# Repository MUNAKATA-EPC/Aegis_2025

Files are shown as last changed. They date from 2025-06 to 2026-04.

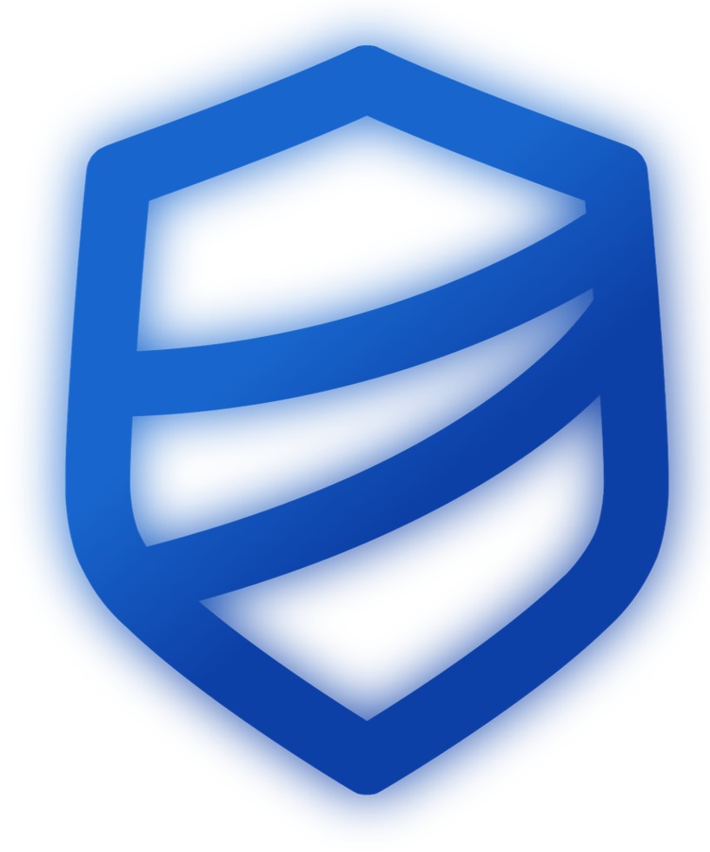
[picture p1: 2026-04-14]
2025/Salvador/presentation sheet material/画像6.jpg

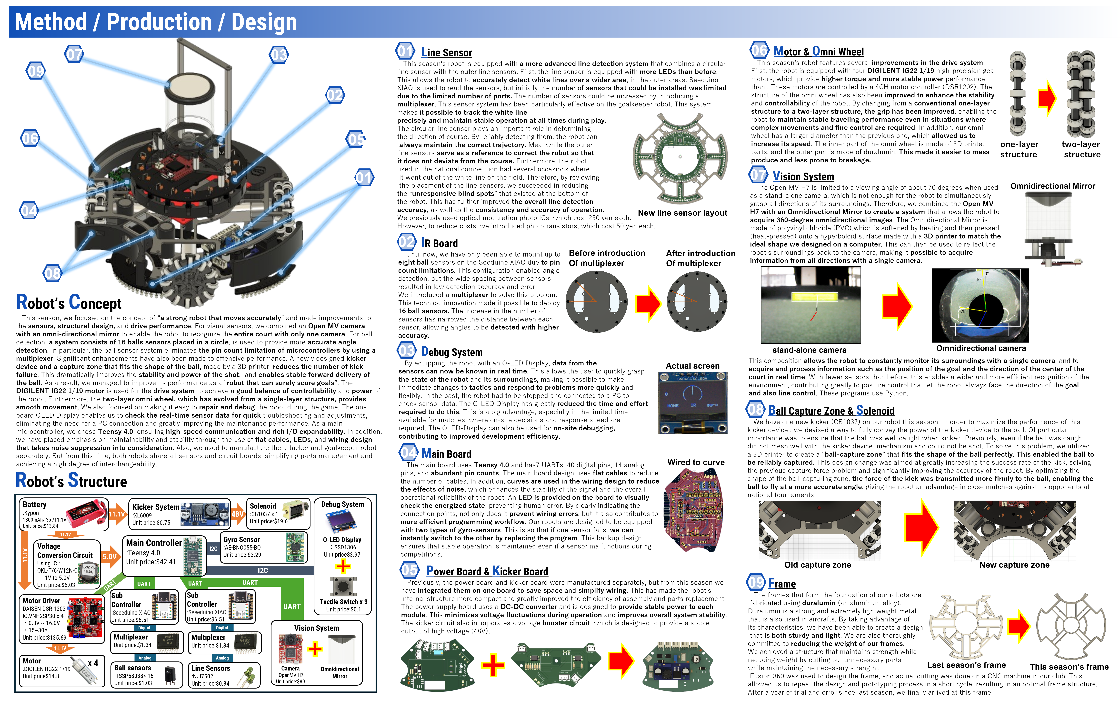
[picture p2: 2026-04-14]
2025/Salvador/presentation sheet material/英語 めっそど.png

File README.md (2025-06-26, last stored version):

🏆 Competition Results

<2024 Season>
Kitakyushu Node Tournament → 🥇 Champion (A Court)

Kyushu Block Tournament → 🥇 Champion, 🏅 Best Presentation Award

Japan Open 2024 Soccer Lightweight League → 31st place

<2025 Season>
Fukuoka Node Tournament → 🥇 Champion

Kyushu Block Tournament → 🥇 Champion

Japan Open 2025 Soccer Lightweight League → 🥇 Champion, 🏅 Best Presentation Award

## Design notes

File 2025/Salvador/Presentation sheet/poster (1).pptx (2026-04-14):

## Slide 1

Munako Artemis
Munakata High School

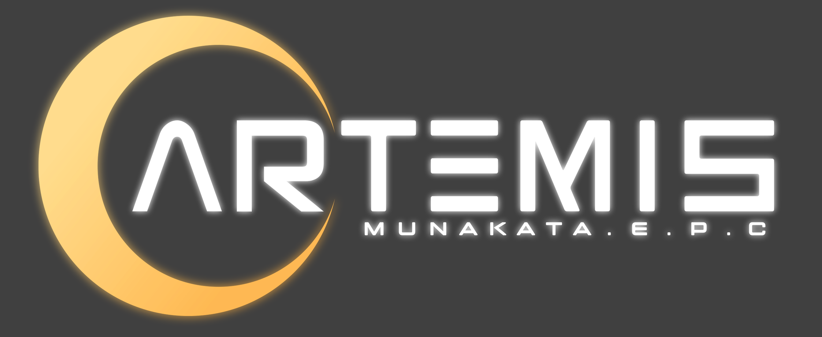
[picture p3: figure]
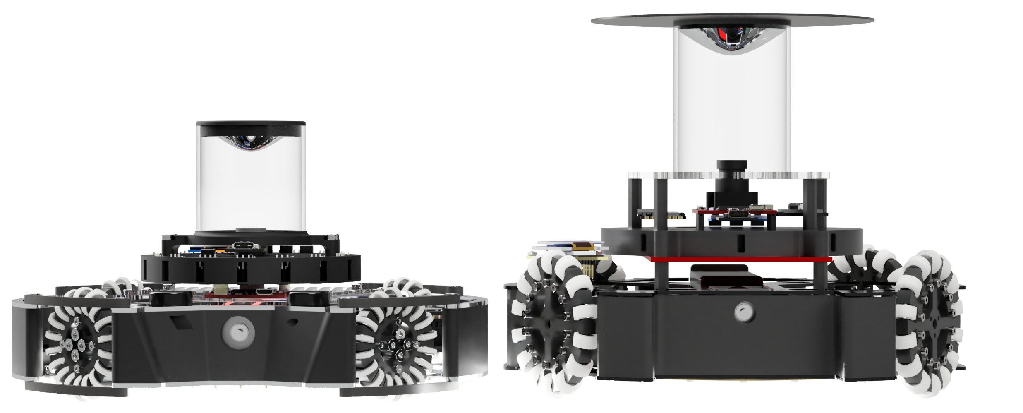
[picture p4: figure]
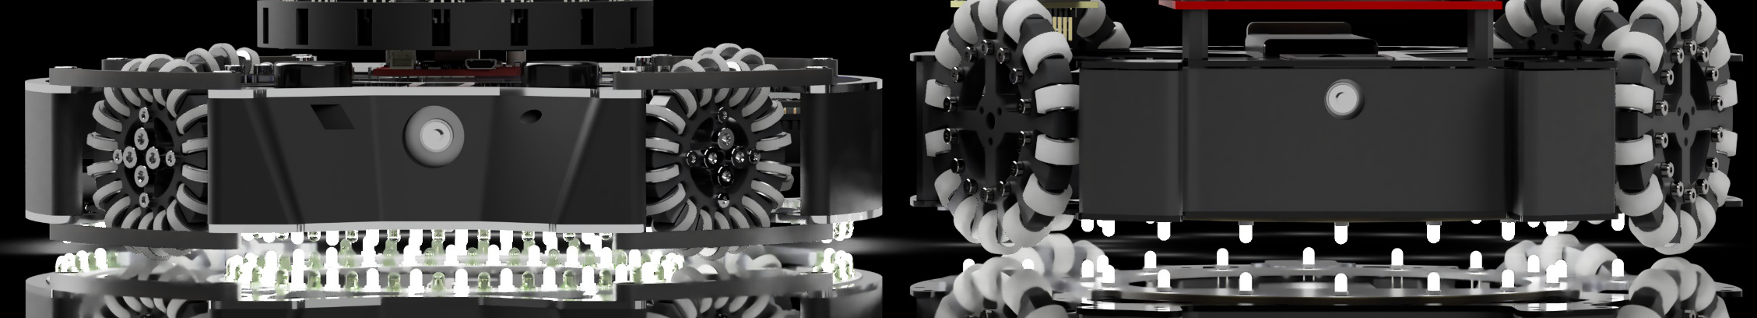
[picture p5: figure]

Abstract

Munako Artemis is a Japanese team participating in Soccer LWL. The team consists of four high school students and has been active since 2021.
For robot design, we mainly use Autodesk Fusion, and for circuit design, we use KiCad. By utilizing 3D printers and CNC milling machines, we efficiently created our robots. Almost all the sensors and microcontrollers are the same among both of our robots, simplifying parts management and increasing compatibility. Additionally, the programming is primarily done in C++ for most microcontrollers and in MicroPython for the camera.
In preparation for the world tournament, we made modifications to our robots to address various issues identified in the Japan Open 2024. One significant problem was the frequent occurrence of out-of-bounds, so we improved the shape of the line sensors from a linear to a circular design and changed the sensor processing algorithm. Additionally, we often had difficulty carrying the ball forward, so we expanded the ball-capturing zone to make it easier to capture the ball and improved the ball-tracking algorithm.
Both of our robots are equipped with a kicker mechanism that uses a solenoid to kick the ball. However, we had no idea which voltage and capacitor capacity would result in the strongest kick. Therefore, we investigated how the kicking power changes with different voltages and capacitor capacities and created graphs to determine the optimal settings for the strongest kick.
Although this is our first time participating in a world tournament, we are strongly motivated by the desire to "interact with various people, acquire diverse knowledge, and gain valuable experiences." To share our knowledge with a wider audience, we have created a website and social media accounts.

REGION

JAPAN

Method / Production / Design

【Robots’ Overview / Descriptions Of The Installed Parts 】

Robot.2's concept is to be a "strong robot with stable operation" for soccer competitions, which is a challenging feat to achieve. However, we have implemented various innovations to achieve this goal.
All components installed in Robot.2 have undergone a year-long development and testing process to ensure stability. Additionally, it is designed to place various additional components for adapting to changes in rules.
By completing the robot production process early and allowing sufficient time for adjustments, we can achieve stable operation and develop a "strong robot".

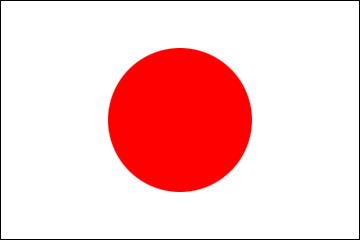
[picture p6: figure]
国旗・国歌」について - 内閣府

LEAGUE

Soccer LWL

Team Member

Kyle Matsuda : Hardware
Yuki Meno : Hardware
Rentaro Ishihara : Software
Ryota Kumadaki : Software

Team Website
https://munako-artemis.github.io/
Team X(Twitter)
https://x.com/munako_artemis
Team GitHub
https://github.com/MUNAKATA-EPC

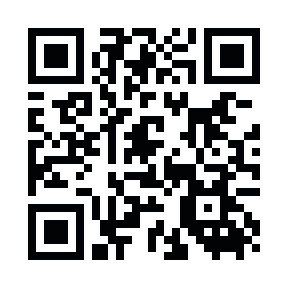
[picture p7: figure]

Website

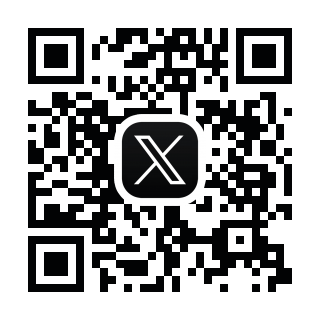
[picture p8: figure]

X(Twitter)

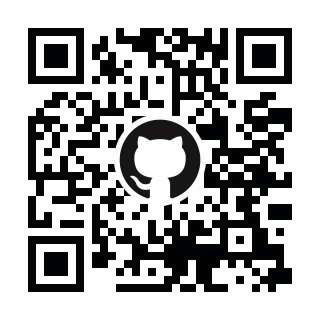
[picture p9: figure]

GitHub

SPONSERS

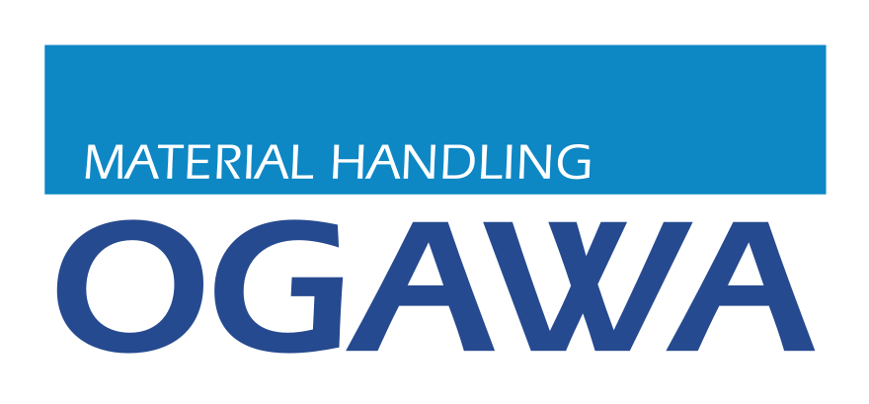
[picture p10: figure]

Robot.1's concept is to be a "robot with a low center of gravity and high maintenance performance". In a robot that moves freely around the court at high speed, having a low center of gravity is crucial. A low center of gravity allows the robot to execute turns and speed changes with minimal force, reducing power consumption and enabling more precise movements.
However, achieving a low center of gravity often means designing the robot to be compact and densely packed with components internally, potentially compromising maintenance accessibility.
To address this challenge, Robot.1 has been designed with a reduced number of components.
Most parts and boards can be quickly removed and replaced, ensuring ease of maintenance despite its low-profile design.

【Robots’ Features】

> Improvement of the shape of the Line Sensor
During the Japan Open 2024, we identified the following issues with our line sensors:
・It was taking too much time for the sensors to detect the white line after the robot has crossed it.
・Poor color compatibility between the sensors and the white line leads to erroneous detections.
To address these issues, we implemented the following improvements.
・Changing the type of the Sensor
As we mentioned earlier, poor color compatibility between the sensors and the white line leaded to erroneous detections, so we have changed the sensor to NJL7502S. By changing the sensor, we can sufficiently detect the difference in response between white and green, enabling us to detect white lines and reduce occurrences of out-of-bounds.
・Changing the shape of the line sensor (Fig.A)
We added new sensors to the left, right, and rear in addition to the central circular line sensor. This allows the robot to immediately detect the white line when it crosses over it.
・Increasing the number of the sensor ports
For the circular line sensor, reading values from each sensor allows us to estimate the current position of the reacting white line.

Fig.A a shape of line sensor
(Robot.1)

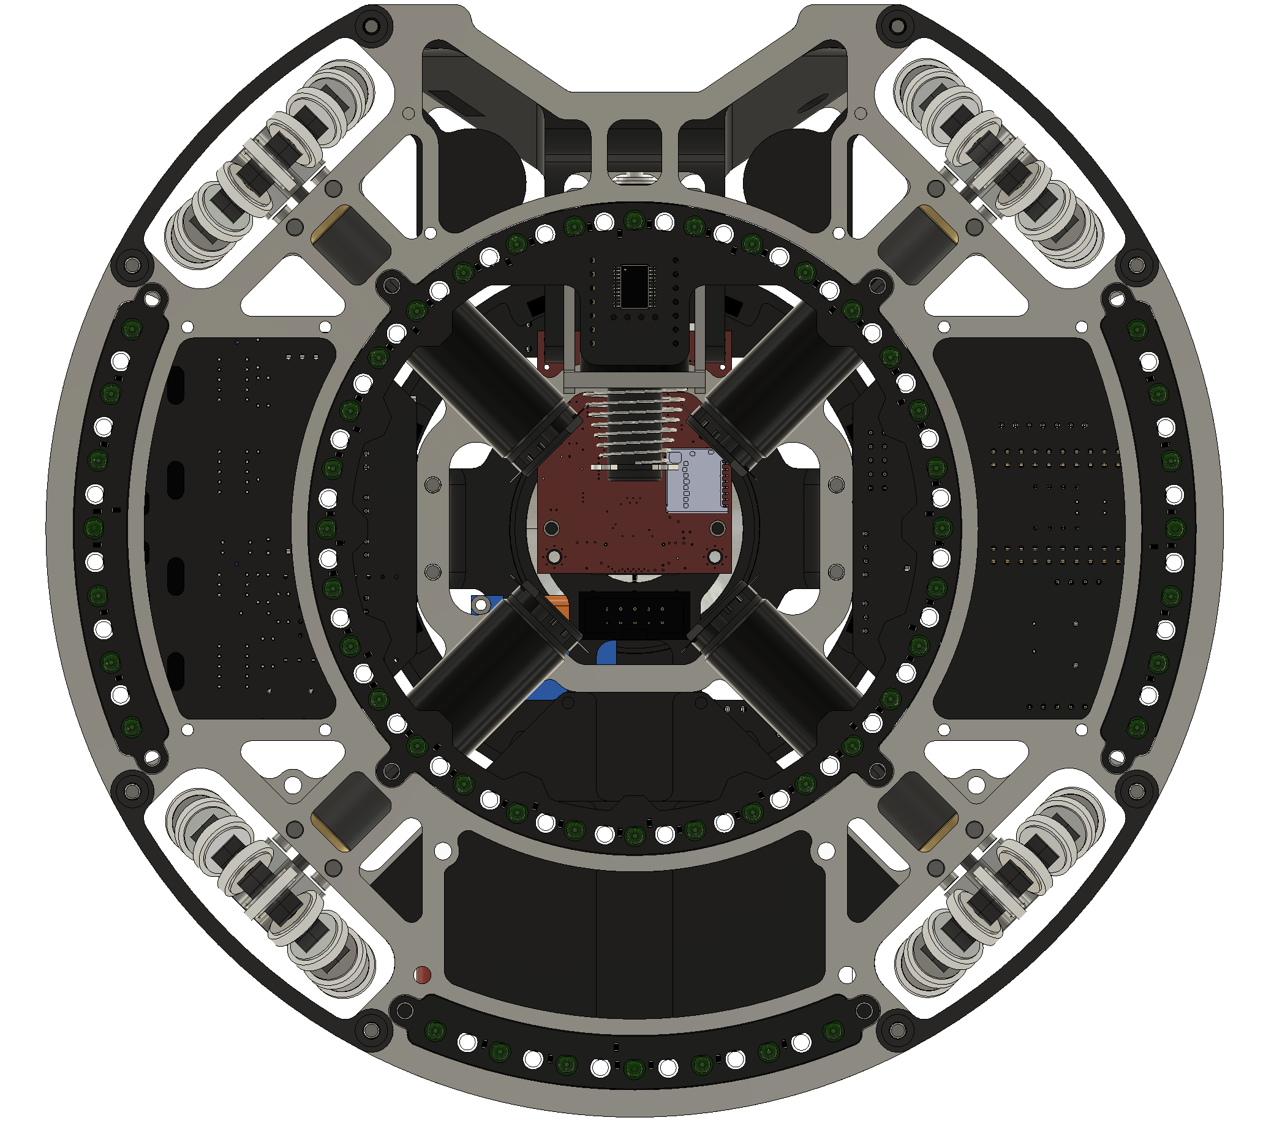
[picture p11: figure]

Ball Angle

Move
Direction

90°

90°

90°

Fig.B-1 ball-tracking system when ball is near

X°

Fig.B-2 ball-tracking system when ball is far

1 Omnidirectional Vision System
We have positioned the camera facing upwards and placed an omnidirectional mirror at the top of an acrylic pipe.
By doing this, we can capture a 360-degree view from the robot without using multiple cameras, significantly simplifying control compared to using multiple cameras.
We are using OpenMV as camera module. It is programmed with MicroPython.

Debugging Components
We have placed menu operation buttons and a small LCD monitor at the rear of the robot.
These are positioned for easy access during a match, allowing us to check sensor values and change the robot’s
Mode without connecting to a computer.

1

Robo.1

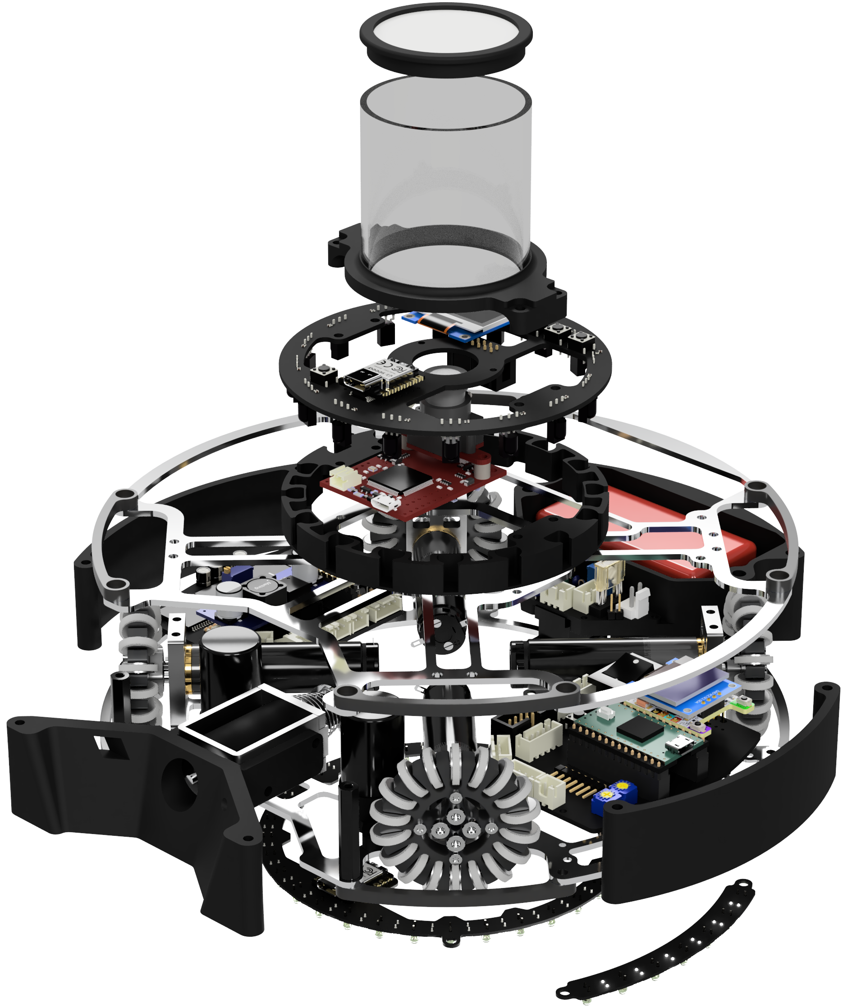
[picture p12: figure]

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
A. Main Board (Robot.1)
This board is equipped with the “Teensy 4.0” main microcontroller, the “BNO055” IMU sensor, the “Twelite UART” communication module for inter-robot communication, the tournament’s official communication module, and various control switches.
All of the data from microcontrollers and sensors on other boards is aggregated here, and this data is used to control the robot.
・Teensy 4.0 : It has many serial ports and very high performance, making it suitable for high-precision control using many sensors and sub-microcontrollers.
・BNO055 : It allows easy control and has less angular drift compared to other IMU sensors.
・Twelite : It enables easy communication by simply connecting it to the microcontroller via UART.

A

3. Ball Capture Detecting Sensor
We have placed an LED on one side of the ball supplement area, and an S4282-51 photodetector IC on the other side, which detects the ball supplement.
This IC responds only to light of a frequency synchronized with the IC itself, allowing it to be used even in daylight or under an indoor lighting without causing false detections, making it ideal for precise control.

4. IR Sensor
We have chosen the TSSP58038 for the ball detection. By placing 16 of them in a circular pattern on the central board, we can calculate the angle of the ball more accurately.

2

3

B. Drive Board (Robot.1)
This board incorporates a motor driver circuit and a kicker drive circuit.
We have chosen VNH5019 for the motor driver IC, and XL6009 for the voltage booster included to de kicker circuit.
The motor driver IC can handle a power supply voltage of up to 41V, which is more than three times the voltage supplied from the battery, and it supports an extremely high current of 30A, ensuring high durability.
The kicker circuit uses two types of MOSFETs, P-channel and N-channel. One is used for controlling the solenoid, and the other is used to disconnect the circuit during the kick motion.
By isolating the kicker circuit from other circuits during kicking, we can physically block the electrical noise caused by the voltage drop during the kicking motion and the back electromotive force generated when the solenoid's shaft returns.
This ensures that no noise affects both the driving power supply and the control power supply.

C. Main Board (Robot.2)
This board is equipped with a Teensy 4.0 as the main microcontroller, an L3GD20H and a BNO055 as IMU sensors, an OpenMV camera, an SSD1306 display, and TSSP58038 sensors for ball detection.
There are eight IR sensors installed to calculate the ball's angle using vector processing.
Two gyro sensors are installed to ensure redundancy in case one fails during the match.
Additionally, the display allows us to check the sensor values and to change the robot's mode without connecting it to a computer, making adjustments to the robot more easily.

B

> Improvement of Ball Access Time
through Ball Tracking Algorithm Enhancement
During the national competition, we identified the following issues with our ball tracking algorithm: Lack of distance-based control between the robot and the ball resulted in excessive rounding, leading to delayed ball access.
To address these issues, we developed the following ball tracking algorithm:
In the diagram on the right, we define Ball Angle as the angle of the ball relative to the robot, and Move Direction as the actual angle of movement of the robot.
A. When the robot is close to the ball (Fig.B-1)
Move in the tangential direction to the ball (= Ball Angle + 90) to approach the ball.
B. When the robot is far from the ball (Fig.B-2)
Add a constant (= Ball Angle + X) to move towards the ball.
By doing these, the robot can approach to it shorter way than before, and colliding with the ball is almost nothing, so own-goal was decreasing.

> Line Tracing Defense Using Circular Line Sensors
Our robot is equipped with circular line sensors, which we utilize for goal defense through line tracing. The defense system is illustrated in Fig.C.
It uses the perpendicular line to the line connecting the two line sensors reacting to the white line as the reference line.
In case ①, when the angle of the ball and the reference line have a small error, the robot stops to block the shot from an oblique direction.
In case ②, when the angle of the ball and the reference line have a large error, the robot moves in the direction of the line sensor detecting the ball, keeping it on the white line while moving towards the ball to block the shot.

By combining these movements in cases ① and ②, the robot can effectively prevent the ball from entering the goal.

Line Sensor
We have positioned a circular board in the center and a board with a circular cut-out shape on the outer edge. The description about the line sensor is summarized in
“Robot’s Feature” section.

6. Power Circuit Board
The power circuit board includes battery protection circuits, and circuits for generating both the drive power supply and control power supply.
The battery protection circuits feature reverse connection protection, overcurrent protection, and over-discharge prevention.
To generate the control power supply, a DC-DC converter is used, which minimizes the electrical noise from the drive power supply, ensuring stable operation of the microcontrollers.

4

5

6

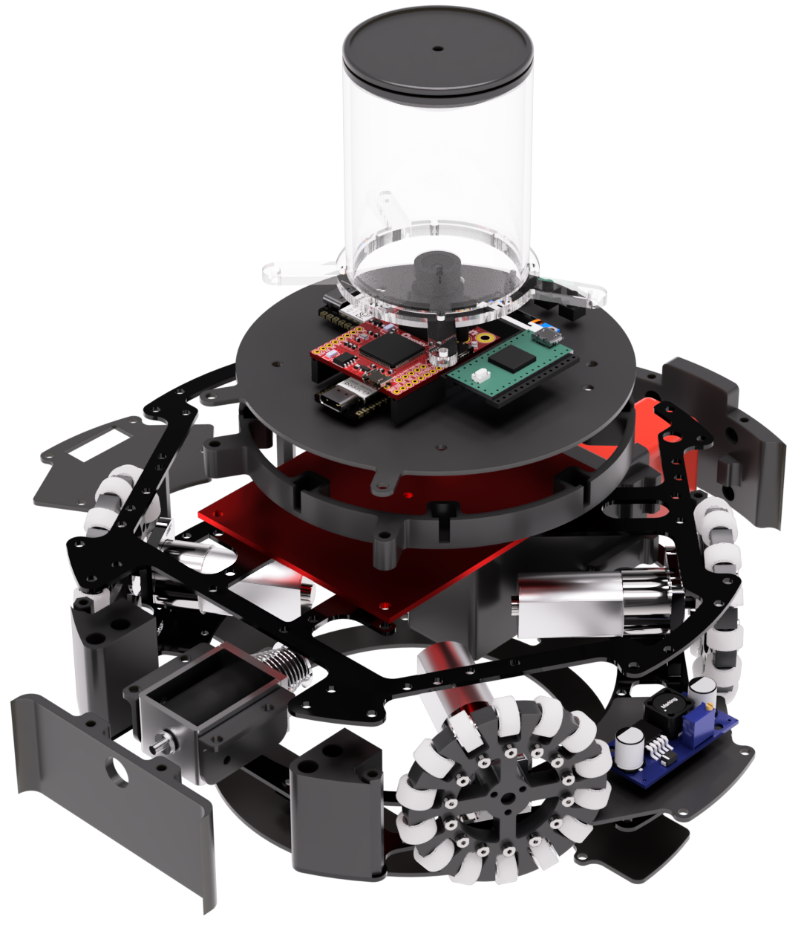
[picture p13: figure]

Robo.2

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
Our Robots’ Structure

Robo.1

Battery
Kypom 3S 11.1V
1300mAh

Gyro Sensor
BNO055

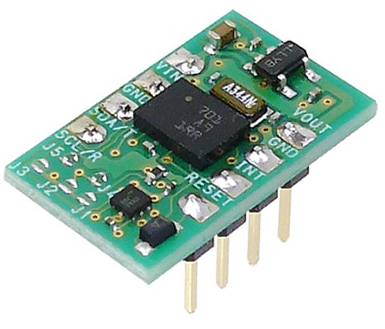
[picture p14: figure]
BNO055使用 9軸センサーフュージョンモジュールキット

11.1V

Voltage Conversion Circuit
Using IC :
OKL-T/6-W12N-C
11.1V to 5.0V

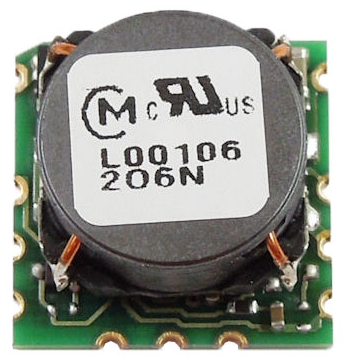
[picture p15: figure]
ムラタ表面実装DC-DCコンバーター OKL-T/6-W12N-C

Drive Circuit Board : Kicker System And Motor Driver

Kicker System
(Please look at
“Kicker System And Research About 　　 Voltage & Capacity Of Capacitors”)

Sub Controller
RP2040 ZERO

Motor Driver
ｘ4
IC : VNH5019A-E

7 Motor
Robot.1 : We use Maxon's RE16 series motors, which offer high efficiency and responsiveness, reducing the robot's power consumption and enabling finer movements.
Robot.2 : We have adopted the DIGILENT IG22 1/19 motor.
Despite being lightweight, it offers high responsiveness and speed.

8. Solenoid
We have selected Takaha's CB1037 solenoid for the kicker.
Among solenoids of similar size in the series, it has a longer stroke and delivers greater kicking force relative to its size, making it ideal for a compact and high-power kicker unit.

7

8

D. Motor Driver : DSR-1202 (Robot.2)
We have adopted the DSR-1202 from the Japanese manufacturer DAISEN. It supports high current and can be easily used by connecting to the microcontroller via UART.

E. Kicker Board (Robot.2)
We use the XL6009 voltage boost IC to step up the voltage to approximately 47V.
For noise reduction, during kicking, we utilize a P channel MOSFET to isolate the kicker circuit from all other circuits, effectively suppressing noise.
The circuit is equipped with two 50V 4700μF charging capacitors.
( For details, check the [ Data / Results / Discussion ] section )

D

E

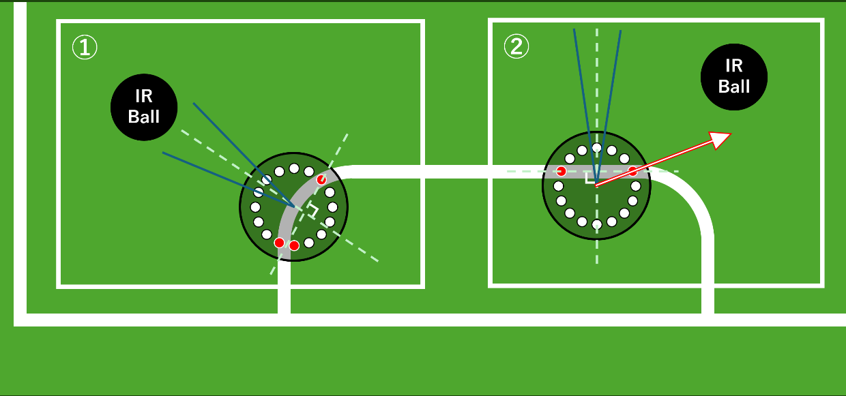
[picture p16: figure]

Fig.C Goal Defense System

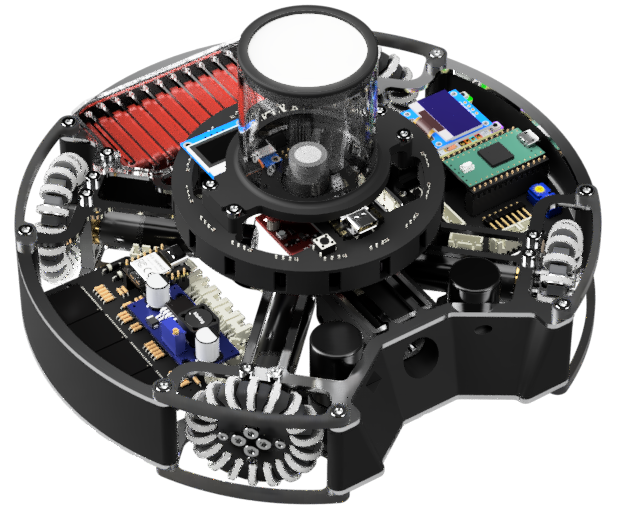
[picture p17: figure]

11.1V

I²C

UART

Main Controller
Teensy 4.0

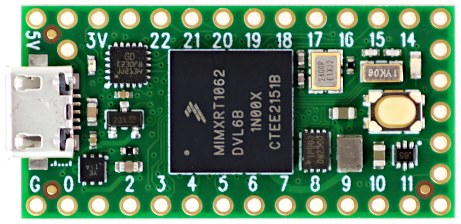
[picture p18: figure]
Teensy® 4.0

5.0V

UART

UART

Sub Controller
Seeeduino Xiao

ANALOG

IR Sensors
TSSP58038 x 16

11.1V

About 48V

9 Frame : A2017
The frame was designed using Autodesk Fusion and machined using a CNC. A2017 Duralumin, known for its excellent durability, allows for a lightweight yet extremely sturdy frame.

Data / Results / Discussion

【About the kicking mechanism and the research about
the voltage and the capacitance of capacitors】
Our robots are equipped with a solenoid which is used for a ball kicking mechanism.
It can kick the ball when you apply high voltage to the solenoid and uses a big capacitance charging capacitor.
The circuit of the kicker mechanism is shown below Fig.1.
However, we had no idea how high the voltage and how big the capacitance of the capacitor should be when we use the solenoid as the kicking system.
Therefore, we decided to research how the kick power will change when we changed the voltage and capacitor capacitance.
<Details Of Research>
Measure the difference of the kicking power when you changed the voltage applied to the solenoid and the capacitance of the capacitor to find the optimal conditions for equipping the solenoid on the robot.
This time we used capacitors from NIPPON CHEMI-CON, Nichicon, Rubycon.
<Research Procedure>
Step 1. make a solenoid drive board which can change the charging capacitor and the
voltage which will be applied to the capacitor.
Step 2. Measure the kick power (*1) by keeping the voltage constant and varying the capacitance of the capacitor.
Step 3. Measure the kick power (*1) by varying the voltage without changing the capacitance.
Step 4. Create a graph based on the experimental data obtained from Step 2 and 3.
(*1) Place a long ruler on the court and kick the ball on it and the kicking power is defined as the distance the ball stopped.

Fig.1. The circuit of the kicker mechanism

9

Team Activities

【Enhancing Team Efficiency through Multiple Workflows】
In team development, the robot production and the software development is difficult to progress at the same time, and this often leads to a single workflow (Fig.6). Given the extremely short preparation period for the world championship, our team found that operating under a single workflow was highly inefficient. Therefore, we proceeded with multiple workflows (Fig.7), which not only allowed us to start working on tasks earlier but also created significant time flexibility.

【Enhancing Team Collaboration with Various Tools】
In our team, we make our collaboration in diverse aspects such as robot design and programming more efficient by using a variety of tools.
All the tools we use are shown below:
・Robot Design : Autodesk Fusion
・Circuit Design : KiCad 6.0 / 7.0
・Programming Tool : Visual Studio Code
(With PlatformIO)
・Source Management : GitHub
(GitHub Desktop)
As a data management tool within our team, we use GitHub (Fig.4).
GitHub is an online source code hosting service where we primarily store files and source code related to robot production. Since these are hosted on the internet, everyone can always access the latest data regardless of location or team member, ensuring that the most current progress is always shared and team development proceeds smoothly.
Additionally, we use GitHub Desktop (Fig.5), a GUI tool, to make using GitHub easier and more understandable compared to the command-line-based Git. We have been using GitHub since 2023. We have published our 2023 season's hardware and software, so please take a look.
Link : https://github.com/MUNAKATA-EPC/Artemis_2023

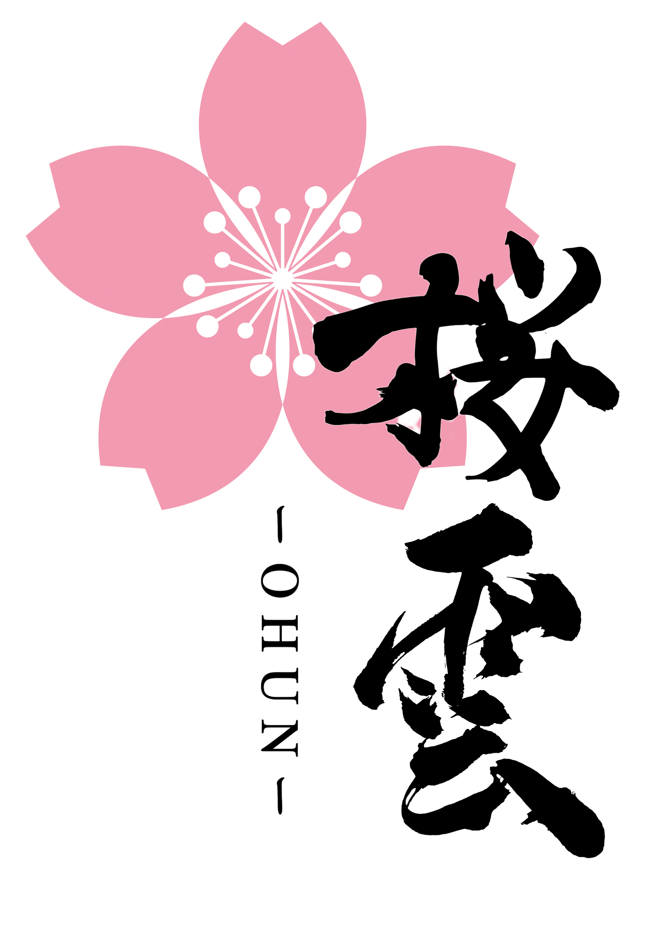
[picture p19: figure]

Vision System

Omnidirectional
Mirror

OpenMV H7 x 1

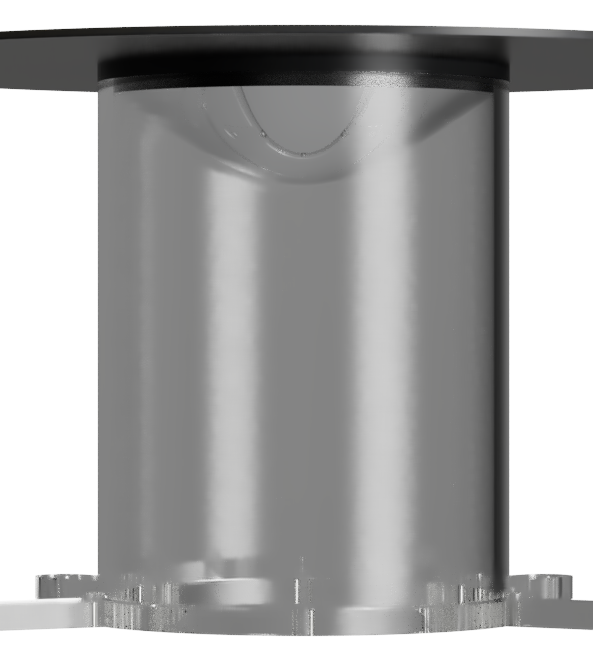
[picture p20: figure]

11.1V

11.1V

Motor Driver
DAISEN DSR-1202

IC:VNH2SP30 x 4
・0.3V ~ 16.0V
・15~30A / channel

Wireless
Communication
Twelite UART

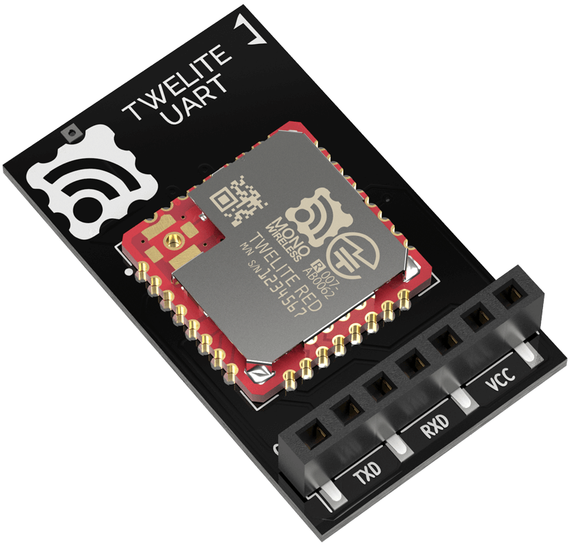
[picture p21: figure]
TWELITE UART-トワイライトユーアート - MONO-WIRELESS.COM

UART

I²C
Digital x 3

Debug System

O-LED
Display
SSD1306 x 1

Tactile Switch x 3
( For switching
robot’s mode)

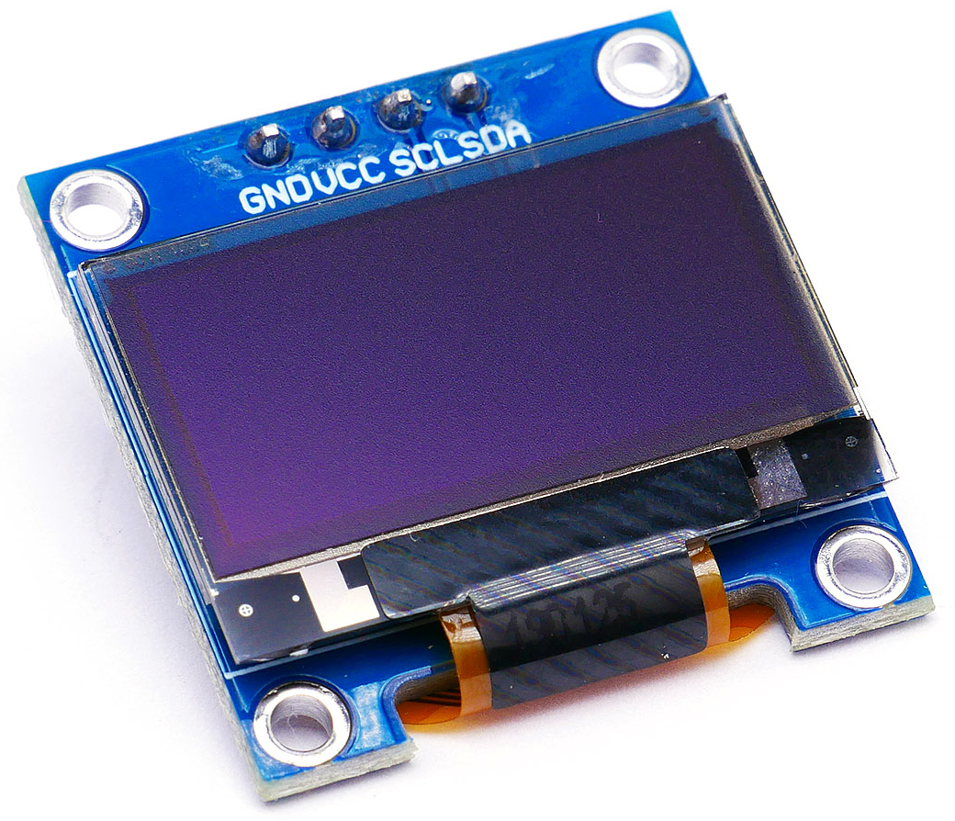
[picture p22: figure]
ESP8255でSSD1306を駆動

Sub Controller
Seeeduino Xiao

Motor
Maxon RE16

X 4

ANALOG

Line Sensors
NJL7502L x 53

Solenoid
CB1037 x 1

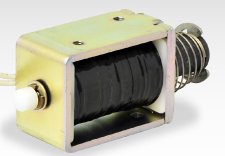
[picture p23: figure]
CB1037 ソレノイドショップ タカハ

FET1 and FET2 are controlled by signals from the microcontroller.
When FET1 is set to HIGH, the connected capacitors (C6, C7) will be charged up. When FET2 is set to HIGH, the solenoid operates using the power stored in the charged capacitors.
Setting FET1 to LOW isolates the kicker circuit from all other circuits using P channel MOSFET, effectively blocking electrical noise.

<Results>
In Fig.2, you can see that the voltage variation and the change in kicking power follow a linear relationship. Similarly, in Fig.3, the change in capacitor capacity and the variation in kicking power also appear to follow a linear relationship.
<Discussion>
Based on these findings, it is considered that higher voltage and larger capacitor capacity lead to greater kicking power. Therefore, we aimed to get as close as possible to the maximum voltage limit allowed by the rules, which is 48V, and selected capacitor capacities based on the available space inside the robot. Robo.1 was equipped with a 6600μF capacitor, and Robo.2 with two 4700μF capacitor, to maximize kicking power as much as possible.

(mm)

(μF)

Autodesk
Fusion

KiCad

GitHub

Google
Spreadsheet

Robo.2

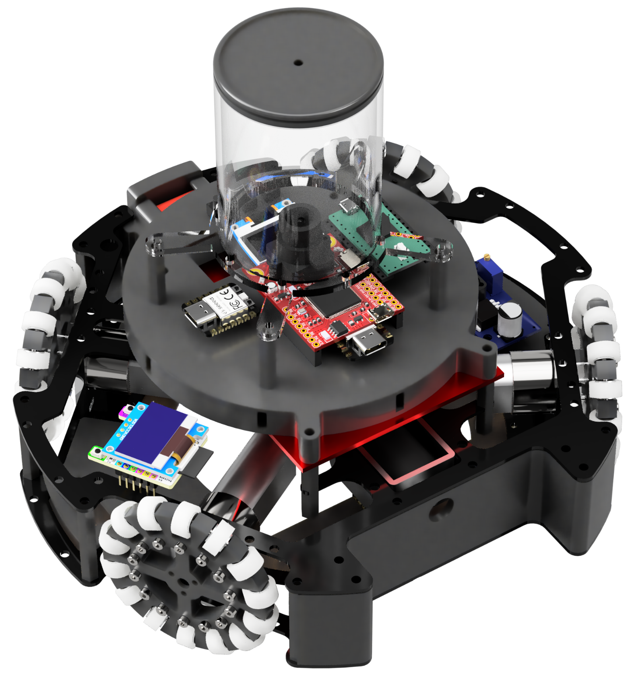
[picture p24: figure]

Battery
Kypom 3S 11.1V
1300mAh

Voltage
Conversion Circuit
Using IC :
OKL-T/6-W12N-C
11.1V to 5.0V

11.1V

UART

Kicker System
(Please look at
“Kicker System And Research About 　　 Voltage & Capacity Of Capacitors”)

Sub Controller
Seeeduino Xiao

About
48V

ANALOG

Solenoid
CB1037 x 1

IR Sensors
TSSP58038 x 16

Visual Studio Code

Discord

Problems:
・Software programmer can’t develop robot’s program until Hardware Engineer finished making them.
・Hardware engineer can’t improve the robots’ problem that is found after finishing making them.

Fig.6 Specific System and Problems of Single Workflow

Robot Design

Circuit Design

Making
Parts

Assembly
Robot

Check
Sensors

Robot Maintenance

Hardware Tasks

Develop
Software Programs

Software Tasks

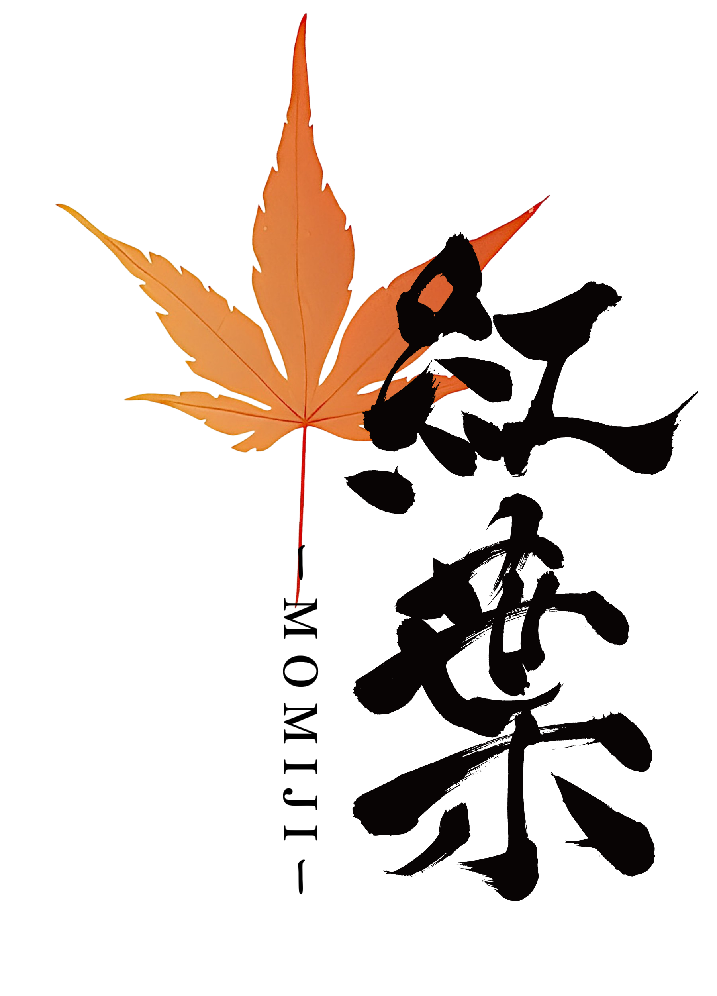
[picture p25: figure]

11.1V

Wireless
Communication
Twelite UART

UART

5.0V

UART

Main Controller
Teensy 4.0

UART

UART

Sub Controller
Seeeduino Xiao

I²C + Digital x 3

Vision System

Omnidirectional
Mirror

OpenMV H7 x 1

Line Sensors
S4282-51 x 22

DIGITAL

Debug System

O-LED
Display
SSD1306 x 1

Tactile Switch x 3
( For switching
robot’s mode)

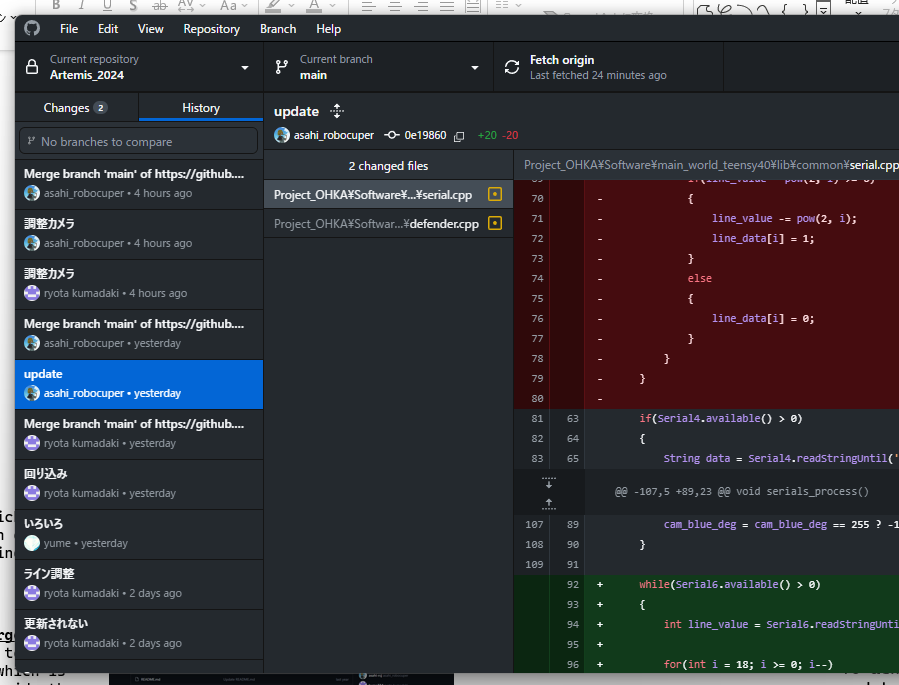
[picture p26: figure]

Fig.7 Specific System and Advantages of Multiple Workflow

Robot Design

Advantages:
・Software programmer
can give feedback about
robots while hardware
engineer is developing.
・We can do software and hardware development at the same time.

Circuit Design

Making
Parts

Feedback

Checking the operation of robots’ parts

Assembly
Robot

Robot Maintenance

Hardware Tasks

Software Tasks

Develop Software Programs

Motor
DIGILENT IG22 1/19

X 4

I²C

Sub Controller
Seeeduino Xiao

Gyro Sensors
L3GD20H
&
BNO055

Fig.4 GitHub(Munako Artemis Season 2024)

Fig.5 GitHub Desktop

To achieve multiple workflows, as we mentioned earlier, we actively used task management tools and communication tools. This allowed the entire team to work on multiple tasks at the same time, thereby enhancing the efficiency of team activities.

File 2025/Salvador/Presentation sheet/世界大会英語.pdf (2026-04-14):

Software; Hardware; Team X; Team GitHub

## 07 Line Sensor

This season‘s robot is equipped with a more advanced line detection system that combines a circular line sensor with the outer line sensors. First, the line sensor is equipped with more LEDs than before. This allows the robot to accurately detect white lines over a wider area, in the outer areas. Seeduino XIAO is used to read the sensors, but initially the number of sensors that could be installed was limited due to the limited number of ports. The number of sensors could be increased by introducing a multiplexer. This sensor system has been particularly effective on the goalkeeper robot. This system makes it possible to track the white line
precisely and maintain stable operation at all times during play.
The circular line sensor plays an important role in determining the direction of
course. By reliably detecting them, the robot can always maintain the correct
trajectory. Meanwhile the outer line sensors serve as a reference to correct the robot so that it does not deviate from the course. Furthermore, the robot used in the national competition had several occasions where it went out of
the white line on the field. Therefore, by reviewing the placement of
the line sensors, we succeeded in reducing the “unresponsive blind spots” that existed at the bottom of the robot. This has further improved the overall
line detection accuracy, as well as the consistency and accuracy of operation. We previously used optical modulation photo ICs, which cost 250 yen each. However, to reduce costs, we introduced phototransistors, which cost 50 yen each.

## 09 Frame

The frames that form the foundation of our robots are fabricated using duralumin (an aluminum alloy). Duralumin is a strong and extremely lightweight metal that is also used in aircrafts. By taking advantage of its characteristics, we have been able to create a design that is both sturdy and light. We are also thoroughly committed to reducing the weight of our frames. We achieved a structure that maintains strength while reducing weight by cutting out unnecessary parts while maintaining the necessary strength . Fusion 360 was used to design the frame, and actual cutting was done on a CNC machine in our club. This allowed us to repeat the design and prototyping process in a short cycle, resulting in an optimal frame structure. After a year of trial and error since last season, we finally arrived at this frame.


## 01 Vision System

The Open MV H7 is limited to a viewing angle of about 70 degrees when used as a stand-alone camera, which is not enough for the robot to simultaneously grasp all directions of its surroundings. Therefore, we combined the Open MV H7 with an Omnidirectional Mirror to create a system that allows the robot to acquire 360-degree omnidirectional images. The Omnidirectional Mirror is made of polyvinyl chloride (PVC),which is softened by heating and then pressed (heat-pressed) onto a hyperboloid surface made with a 3D printer to match the ideal shape we designed on a computer. This can then be used to reflect the robot’s surroundings back to the camera, making it possible to acquire information from all directions with a single camera.

# Robot’s Concept

This season, we focused on the concept of “a strong robot that moves accurately” and made improvements to the sensors, structural design, and drive performance. For visual sensors, we combined an Open MV camera with an omni-directional mirror to enable the robot to recognize the entire court with only one camera. For ball detection, a system consists of 16 balls sensors placed in a circle, is used to provide more accurate angle detection. In particular, the ball sensor system eliminates the pin count limitation of microcontrollers by using a multiplexer. Significant enhancements have also been made to offensive performance. A newly designed kicker device and a capture zone that fits the shape of the ball, made by a 3D printer, reduces the number of kick failure. This dramatically improves the stability and power of the shot, and enables stable forward delivery of the ball. As a result, we managed to improve its performance as a "robot that can surely score goals”. The DIGILENT IG22 1/19 motor is used for the drive system to achieve a good balance of controllability and power of the robot. Furthermore, the two-layer omni wheel, which has evolved from a single-layer structure, provides smooth movement. We also focused on making it easy to repair and debug the robot during the game. The on-board OLED Display enables us to check the real-time sensor data for quick troubleshooting and adjustments, eliminating the need for a PC connection and greatly improving the maintenance performance. As a main microcontroller, we chosen Teensy 4.0, ensuring high-speed communication and rich I/O expandability. In addition, we have placed emphasis on maintainability and stability through the use of flat cables, LEDs, and wiring design that takes noise suppression into consideration. Also, we used to manufacture the attacker and goalkeeper robot separately. But from this time, both robots share all sensors and circuit boards, simplifying parts management and achieving a high degree of interchangeability.

I2C

# Method / Production / Design

# Munako Aegis

# Soccer LWL

# League

# JAPAN

# Munakata High School

# Team Name

# Our School

# Region

# Abstract

# Maiki Kimura

# Umi Fujita

# Yuta Kurisaki

# Koki Suehiro

# Team Member

Aircraft and Circuit Design Manager

Goalkeeper Program Manager

Attacker Program Manager

# Sponsor

Circuit Design, Media
Manager

# Smoothing Sensor Readings Using Moving Average

There were some fluctuations in the analog values from the ball sensor. To reduce this, we applied a moving average filter to the sensor readings. We rolled the ball away from the sensor and observed the changes in the readings. We analyzed how the variation changed with different numbers of moving average samples and finally chose 10 samples. The graph below compares the results with and without the moving average.
Result：

The graph shows that applying a moving average filter makes the sensor readings smoother. Based on this result, we also applied the moving average to the analog values of the line sensor, not just the ball sensor.

11.1V

Omnidirectional Mirror

### one-layer structure

### two-layer structure

We are “Munako Aegis,” a team of four Japanese high school students competing in the Lightweight League.
We began our activities in the 2023 season and have been steadily improving our skills through daily, dedicated work on our robot.

When we first started, none of us had any specialized skills. However, we tackled mechanical design, programming, and circuit design every day, gaining knowledge and experience through trial and error. In our first year, we placed first in the preliminary competition and qualified for the Japan Open. However, we finished a disappointing 31st out of 64 teams in the main event.
Nevertheless, we didn't give up and kept working hard. This year, we won first place at the Japan Open. We also won the Best Presentation Award.

We primarily use Autodesk Fusion for mechanical design and KiCad for circuit design. For fabrication, we utilize 3D printers and CNC milling machines to develop robots efficiently and with high precision.
We write programs in Visual Studio Code, using C++ for the microcontroller and Micro Python for camera control, developed with the Open MV IDE.

Our robot uses duralumin for its body to combine light weight with high durability. We made exterior components, such as the battery box and side covers, ourselves using a 3D printer, allowing for design flexibility. For the circuit board, we asked our sponsor, JLCPCB, to fabricate it with high precision to achieve a stable circuit configuration.
The camera system uses an Omnidirectional Mirror, which we made ourselves by heat-pressing vinyl chloride. This allows a single camera to provide a 360-degree field of view while significantly reducing costs. In addition, a kicker mechanism is installed using a solenoid provided by TAKAHA.

To address the “line-out” issue that many teams have struggled with in recent years, we incorporated speed control.
The robot measures its speed in real time as it moves and runs at the optimum speed according to its court position to prevent line-outs at the fastest possible speed.
In addition, we use a double-structured omni wheel design. The double structure increases the ground contact area with the floor and improves braking ability.
Red LEDs are used for the line sensor to improve response speed and accuracy. These innovations strengthen the line area.

For ball detection, we use a multiplexer to handle multiple inputs despite a limited number of pins, and we stabilize noisy values using moving average processing. In addition, an LCD monitor allows the user to check various values in real time without connecting to a PC.

In preparation for the world championships, we reviewed our robot’s design. The shape of the robot, which used to differ between the attacker and the goalkeeper, is now unified. By adopting two identical robots that combine the advantages of both roles, it is now possible to switch roles immediately during a match. Furthermore, all sensors and circuit boards are also standardized, resulting in improved parts
management and even higher compatibility. You can follow our activities on X (formerly Twitter). We also publish all our data on GitHub.

11.1V

### Battery

:Kypon
1300mAh/ 3s /11.1V
Unit price:$13.84

11.1V

Multiplexer
Unit price:$1.34

Digital

Analog

## Main Controller

:Teensy 4.0
Unit price:$42.41

Sub
Controller
:Seeeduino XIAO
Unit price:$6.51

Multiplexer
Unit price:$1.34

Ball sensors
:TSSP58038× 16
Unit price:$1.03

Solenoid
:CB1037 x 1
Unit price:$19.6

Motor
:DIGILENTIG22 1/19
Unit price$14.8

X 4

Motor Driver
DAISEN DSR-1202
IC:VNH2SP30 x 4
・0.3V ~ 16.0V
・15~30A
Unit price:$135.69

Gyro Sensor
:AE-BNO055-BO
Unit price:$3.29

### Kicker System

:XL6009
Unit price:$0.75
11.1V | 48V

5.0V

UART | UART

Digital

I2C

UART

Voltage
Conversion Circuit
Using IC :
OKL-T/6-W12N-C
11.1V to 5.0V
Unit price:$6.03

Analog

Sub
Controller
:Seeeduino XIAO
Unit price:$6.51

Line Sensors
:NJI7502
Unit price:$0.34

Debug System

O-LED Display
：SSD1306
Unit price$3.97

Tactile Switch x 3
Unit price:$0.1

# Robot’s Structure

Vision System

Omnidirectional
Mirror

Camera
:OpenMV H7
Unit price:$80

UART

The motors we used on the robot last season
were 6-volt motors, which limited its speed and performance. So we decided to look for faster and more efficient motors. While keeping costs as low as possible, we chose 12-volt motors. As a result, we came up with the following motor options.
・ DC geared motor 12V 1:19（DIGILENT IG22 1/19）
（ about 19 dollars ）June 2024 This motor had the performance we were looking for and
we thought it was a good choice. However, while this motor increased the speed, it caused more out of bounds.
So, even if the robot is fast, it's meaningless if it goes out of bounds.
In the past, the motor speed was reduced to prevent out of bounds,
but there was a problem with the motor continuing to accelerate as it was. To solve this problem, we decided to use the BNO055 to measure the robot‘s speed. This allows us to reduce its speed near the boundary lines to prevent out-of-bounds, while allowing it to reach maximum speed at the center of the court.
Experimental environment
For the Verification 1 and Verification 2 experiments, we ran the robot from one end of the court to the other and used a recording timer to measure the distance traveled every 0.1 second. Based on these measurements, we calculated the average speed for each 0.1-second interval and created a graph showing how the speed changed over time. （See Photos 1 and 2）

「 Speed control 」
determine the set speed. If the measured speed is below the set speed, increase the motor power. Conversely, if the speed exceeds the set speed, decrease the motor power.
This method is called "speed control."（See Figure 1） We conducted the following verification to evaluate whether this method is effective in preventing out of bounds.

Verification 1:
Exploring the difference between speed control and no control. To verify that the speed control was functioning correctly, we conducted experiments both with and without speed control.
Next, we compared the relationship between velocity (v: cm/s) and time (t: seconds) using graphs.
Result：

The graph shows that the speed is constant at 80 cm/s with speed control compared to without.

Verification 2:
Comparison of Deceleration Characteristics With and Without Speed Control.
The graph compares the relationship between velocity (v: cm/s) and time (t: seconds) in two cases. In the first case, the robot was accelerated to a set speed using speed control, and then decelerated by reducing that set speed. In the second case, the robot was operated without speed control at a fixed PWM value for a certain time, and then decelerated by reducing the PWM value.
Result：

The graph shows a case where the final speeds after deceleration are approximately equal with and without speed control. In this example, the time required to decelerate to the set speed is shorter with speed control than without it, even though the initial speed was higher with speed control. This indicates that speed control is more effective for deceleration. (See Graph 2)

Verification 3:
Find the maximum value of the speed that is not out of bounds
The goal was to find the maximum speed at which the robot could stop without going out of bounds and hitting a wall when stepping on the line. We created a program to brake when stepping on the line, varied the set speed, and recorded the maximum speed that did not go out of bounds.

The results show that a set speed of 600 is the maximum optimal speed at which the robot can stop without going out of bounds. Therefore, this speed was set as the maximum speed when near the line. In other areas , we decided to use speed control with no upper speed limit.
(See Table 1)
For position estimation, a camera is used to estimate the position of the robot based on the direction of the center of the court.

Conclusion：
From Verification 1, it was observed that without speed control, the robot’s speed continues to increase, whereas with speed control, the speed eventually stabilizes.
From Verification 2, it was shown that the motor with speed control decelerates more quickly than the one without it.
From Verification 3, the maximum speed at which the robot can stop without going out of bounds was identified. Previously, this speed had been manually adjusted through trial and error.

## Comparison of Speeds Without Going Out of Bounds

▷Photo１ The experiment scene | ▷Photo２ The experiment scene

# Speed control that leads to improved line control

▷Fig2

# Data / Results / Discussion

### Verification1

### Verification2

### Verification3

### Speed instability

Slow deceleration | Quick deceleration Speed stability
Unclear maximum speed | Clear maximum speed

## As a result of this test, the following is now possible

## Set speed

### Fast

### Slow

▷Fig1 Mechanism of speed control

▷Gragh2

▷Gragh1

## Effect of Speed Control on Deceleration

## Effect of Speed Control on Velocity Stability

Effect of a Moving Average Filter | ▷Gragh3

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
# Robot 1,2

Actual screen

stand-alone camera | Omnidirectional camera

Before introduction
Of multiplexer

After introduction
Of multiplexer

Wired to curve

Old capture zone | New capture zone

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
0 | 0.5 | 1 | 1.5 | 2 | 2.5
| with speed control
| without speed control

(v: cm/s)

(t: seconds)

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
0 | 0.5 | 1 | 1.5 | 2 | 2.5
| with speed control
| without speed control

(v: cm/s)

(t: seconds)

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
without the moving average filter

with the moving average filter

Analog value

Number of readings

# Evaluation of Optimal LED Color for Line Sensors

Our line sensors have been using white LEDs until now, We decided to experiment with the question of whether white LEDs are really suitable. We are using full-color LEDs in the experiment that can change the color and brightness of the light. We made a graph and a table of the data when the robot passed a white line using red, green, and blue light compared to the white light we had used before.

Looking at Figure 1, it’s easy to assume that white light is advantageous because the response values are high. However, it’s also evident that the values when there is no response are higher compared to those of other colors.
For line sensors, a greater difference between the minimum and maximum values is more advantageous. Comparing the differences in Figure 2, red and blue show a larger range than the other two colors. However, blue is a prohibited color and cannot be used.
Therefore, it can be concluded that the most suitable light source for the sensor is red.
Response Values by Color | Max-Min Difference for Each Color
▷Gragh4 | ▷Gragh5

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
white
red
green
blue
0 | 100 | 200 | 300

blue

green

red

white

# 今田 耕司様

## 08 Ball Capture Zone & solenoid

We have one new kicker (CB1037) on our robot this season. In order to maximize the performance of this kicker device , we devised a way to fully convey the power of the kicker device to the ball. Of particular importance was to ensure that the ball was well caught when kicked. Previously, even if the ball was caught, it did not mesh well with the kicker device mechanism and could not be shot. To solve this problem, we utilized a 3D printer to create a “ball-capture zone” that fits the shape of the ball perfectly. This enabled the ball to be reliably captured. This design change was aimed at greatly increasing the success rate of the kick, solving the previous capture force problem and significantly improving the accuracy of the robot. By optimizing the shape of the ball-capturing zone, the force of the kick was transmitted more firmly to the ball, enabling the ball to fly at a more accurate angle, giving the robot an advantage in close matches against its opponents at national tournaments.

## 06 Motor & Omni Wheel

This season's robot features several improvements in the drive system. First, the robot is equipped with four DIGILENT IG22 1/19 high-precision gear motors, which provide higher torque and more stable power performance than . These motors are controlled by a 4CH motor controller (DSR1202). The structure of the omni wheel has also been improved to enhance the stability and controllability of the robot. By changing from a conventional one-layer structure to a two-layer structure, the grip has been improved, enabling the robot to maintain stable traveling performance even in situations where complex movements and fine control are required. In addition, our omni wheel has a larger diameter than the previous one, which allowed us to increase its speed. The inner part of the omni wheel is made of 3D printed parts, and the outer part is made of duralumin. This made it easier to mass produce and less prone to breakage.

## 02 Debug System

By equipping the robot with an O-LED Display, data from the
sensors can now be known in real time. This allows the user to quickly grasp the state of the robot and its surroundings, making it possible to make immediate changes to tactics and respond to problems more quickly and flexibly. In the past, the robot had to be stopped and connected to a PC to check sensor data. The O-LED Display has greatly reduced the time and effort required to do this. This is a big advantage, especially in the limited time available for matches, where on-site decisions and response speed are required. The OLED-Display can also be used for on-site debugging, contributing to improved development efficiency.

## 03IR Board

Until now, we have only been able to mount up to eight ball sensors on the Seeduino XIAO due to pin count limitations. This configuration enabled angle detection, but the wide spacing between sensors resulted in low detection accuracy and error. We introduced a multiplexer to solve this problem. This technical innovation made it possible to deploy

### 16 ball sensors. The increase in the number of

sensors has narrowed the distance between each sensor, allowing angles to be detected with higher accuracy.

## 04 Main Board

The main board uses Teensy 4.0 and has7 UARTs, 40 digital pins, 14 analog pins, and abundant pin counts. The main board design uses flat cables to reduce the number of cables. In addition, curves are used in the wiring design to reduce the effects of noise, which enhances the stability of the signal and the overall operational reliability of the robot. An LED is provided on the board to visually check the energized state, preventing human error. By clearly indicating the connection points, not only does it prevent wiring errors, but it also contributes to more efficient programming workflow. Our robots are designed to be equipped with two types of gyro-sensors. This is so that if one sensor fails, we can instantly switch to the other by replacing the program. This backup design ensures that stable operation is maintained even if a sensor malfunctions during competitions.

## 05 Power Board & Kicker Board

Previously, the power board and kicker board were manufactured separately, but from this season we have integrated them on one board to save space and simplify wiring. This has made the robot's internal structure more compact and greatly improved the efficiency of assembly and parts replacement. The power supply board uses a DC-DC converter and is designed to provide stable power to each module. This minimizes voltage fluctuations during operation and improves overall system stability. The kicker circuit also incorporates a voltage booster circuit, which is designed to provide a stable output of high voltage (48V).

# Team Activities

・KiCad
Used for circuit
fabrication

Our team mainly uses the following software.

・ GitHub
Used for data
storage

・ Visual Studio
Used for programming
(except for the camera)
with C++

## Design

・Autodesk Fusion
Used for designing
the robot’s frame and
components

## Program

・ OpenMV IDE
Used for programming
the camera with Python

・ Discord
Used for sharing
information among team
members

## Management

# Tool

0

20000

40000

60000

80000

100000

120000

140000

160000

180000

200000

min | robot effort

Our team has been participating in the RoboCup Soccer Lightweight League since last season, making this our second year together. The team consists of four members — three of whom have been involved in robot competitions since high school, and one since junior high school. Despite being a relatively new team, we have set a major goal of "winning the world championship," and we’ve been working hard every day to build our robots and improve our technical skills. Given our limited time, we established a clear activity policy to ensure that every team member could grow steadily. In this presentation, we would like to introduce the policies we followed and how we advanced our activities based on them.

Each team
member built
their own robot,
deepening their
understanding of
its structure and
mechanisms.

## First year (first half)

Through the process
of building robots,
we identified our
own strengths and
weaknesses and
assigned team roles
accordingly.

## First year (second half)

Reflecting on our experience at the Japan Open, we discussed the mechanisms we wanted to implement, examined the
necessary technologies, created a plan, and clarified each step to steadily improve our technical skills.

## Second year (first half) Second year (second half)

## For the World Championship

## winning the World Championship

Based on our past match
experiences, we discussed
additional mechanisms and
strategies we wanted to
implement, and as a team, we talked about what preparations were necessary for the upcoming competition.

## Goal

Based on our
experience at the
Japan Open, we
discussed what we
need to do to adapt
to the environment of
the World
Championship.

# Ⅾaily accumulation and planning are important

In order to enhance our technical skills, we have dedicated an enormous amount of time and made continuous, extraordinary efforts. On weekends, we work from 10 a.m. to 5 p.m., and on weekdays, we usually continue activities from 4 p.m. to 7 p.m. after school. The graph on the right shows the cumulative number of hours we’ve spent on robot development, broken down by month. The vertical axis represents the time spent working on the robot (in minutes), and the horizontal axis represents the progression of dates. This graph is a record of our relentless efforts to aim for the world stage, despite having limited time.

Our total activity time amounts to approximately 180,000 minutes — or about 3,140 hours.

This massive amount of time is proof of our wholehearted belief that “small efforts every day will eventually lead to great achievements. ”Through our journey, we have not only built robots — we’ve also developed the very ability to persevere as a team. Because we experienced both failure and success with our own hands, we’ve come to truly understand that continued effort leads to growth and results — and ultimately to building stronger robots.

New line sensor layout

This composition allows the robot to constantly monitor its surroundings with a single camera, and to acquire and process
information such as the position of the goal and the direction of the center of the court in real time. With fewer sensors than before,
this enables a wider and more efficient recognition of the environment, contributing greatly to posture control that let the robot always face the direction of the goal and also line control. These programs use Python.

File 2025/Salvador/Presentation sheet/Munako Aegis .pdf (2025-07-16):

Software; Hardware; Team X; Team GitHub

## 06 Motor & Omni Wheel

This season's robot features several improvements in the drive system. First, the robot is equipped with four DIGILENT IG22 1/19 high-precision gear motors, which provide higher torque and more stable power performance than . These motors are controlled by a 4CH motor controller (DSR1202). The structure of the omni wheel has also been improved to enhance the stability and controllability of the robot. By changing from a conventional one-layer structure to a two-layer structure, the grip has been improved, enabling the robot to maintain stable traveling performance even in situations where complex movements and fine control are required. In addition, our omni wheel has a larger diameter than the previous one, which allowed us to increase its speed. The inner part of the omni wheel is made of 3D printed parts, and the outer part is made of duralumin. This made it easier to mass produce and less prone to breakage.

## 07 Vision System

The Open MV H7 is limited to a viewing angle of about 70 degrees when used as a stand-alone camera, which is not enough for the robot to simultaneously grasp all directions of its surroundings. Therefore, we combined the Open MV H7 with an Omnidirectional Mirror to create a system that allows the robot to acquire 360-degree omnidirectional images. The Omnidirectional Mirror is made of polyvinyl chloride (PVC),which is softened by heating and then pressed (heat-pressed) onto a hyperboloid surface made with a 3D printer to match the ideal shape we designed on a computer. This can then be used to reflect the robot’s surroundings back to the camera, making it possible to acquire information from all directions with a single camera.

## 08 Ball Capture Zone & Solenoid

We have one new kicker (CB1037) on our robot this season. In order to maximize the performance of this kicker device , we devised a way to fully convey the power of the kicker device to the ball. Of particular importance was to ensure that the ball was well caught when kicked. Previously, even if the ball was caught, it did not mesh well with the kicker device mechanism and could not be shot. To solve this problem, we utilized a 3D printer to create a “ball-capture zone” that fits the shape of the ball perfectly. This enabled the ball to be reliably captured. This design change was aimed at greatly increasing the success rate of the kick, solving the previous capture force problem and significantly improving the accuracy of the robot. By optimizing the shape of the ball-capturing zone, the force of the kick was transmitted more firmly to the ball, enabling the ball to fly at a more accurate angle, giving the robot an advantage in close matches against its opponents at national tournaments.

## 09 Frame

The frames that form the foundation of our robots are fabricated using duralumin (an aluminum alloy). Duralumin is a strong and extremely lightweight metal that is also used in aircrafts. By taking advantage of its characteristics, we have been able to create a design that is both sturdy and light. We are also thoroughly committed to reducing the weight of our frames.
We achieved a structure that maintains strength while
reducing weight by cutting out unnecessary parts
while maintaining the necessary strength .
Fusion 360 was used to design the frame, and actual cutting was done on a CNC machine in our club. This allowed us to repeat the design and prototyping process in a short cycle, resulting in an optimal frame structure. After a year of trial and error since last season, we finally arrived at this frame.


## 05 Power Board & Kicker Board

Previously, the power board and kicker board were manufactured separately, but from this season we have integrated them on one board to save space and simplify wiring. This has made the robot's internal structure more compact and greatly improved the efficiency of assembly and parts replacement. The power supply board uses a DC-DC converter and is designed to provide stable power to each module. This minimizes voltage fluctuations during operation and improves overall system stability. The kicker circuit also incorporates a voltage booster circuit, which is designed to provide a stable output of high voltage (48V).

## 04 Main Board

The main board uses Teensy 4.0 and has7 UARTs, 40 digital pins, 14 analog pins, and abundant pin counts. The main board design uses flat cables to reduce the number of cables. In addition, curves are used in the wiring design to reduce the effects of noise, which enhances the stability of the signal and the overall operational reliability of the robot. An LED is provided on the board to visually check the energized state, preventing human error. By clearly indicating the connection points, not only does it prevent wiring errors, but it also contributes to more efficient programming workflow. Our robots are designed to be equipped with two types of gyro-sensors. This is so that if one sensor fails, we can instantly switch to the other by replacing the program. This backup design ensures that stable operation is maintained even if a sensor malfunctions during competitions.

## 03 Debug System

By equipping the robot with an O-LED Display, data from the
sensors can now be known in real time. This allows the user to quickly grasp the state of the robot and its surroundings, making it possible to make immediate changes to tactics and respond to problems more quickly and flexibly. In the past, the robot had to be stopped and connected to a PC to check sensor data. The O-LED Display has greatly reduced the time and effort required to do this. This is a big advantage, especially in the limited time available for matches, where on-site decisions and response speed are required. The OLED-Display can also be used for on-site debugging, contributing to improved development efficiency.

## 02 IR Board

Until now, we have only been able to mount up to eight ball sensors on the Seeduino XIAO due to pin count limitations. This configuration enabled angle detection, but the wide spacing between sensors resulted in low detection accuracy and error.
We introduced a multiplexer to solve this problem. This technical innovation made it possible to deploy

### 16 ball sensors. The increase in the number of

sensors has narrowed the distance between each sensor, allowing angles to be detected with higher accuracy.

This composition allows the robot to constantly monitor its surroundings with a single camera, and to acquire and process information such as the position of the goal and the direction of the center of the court in real time. With fewer sensors than before, this enables a wider and more efficient recognition of the environment, contributing greatly to posture control that let the robot always face the direction of the goal and also line control. These programs use Python.

# Robot’s Concept

This season, we focused on the concept of “a strong robot that moves accurately” and made improvements to the sensors, structural design, and drive performance. For visual sensors, we combined an Open MV camera with an omni-directional mirror to enable the robot to recognize the entire court with only one camera. For ball detection, a system consists of 16 balls sensors placed in a circle, is used to provide more accurate angle detection. In particular, the ball sensor system eliminates the pin count limitation of microcontrollers by using a multiplexer. Significant enhancements have also been made to offensive performance. A newly designed kicker device and a capture zone that fits the shape of the ball, made by a 3D printer, reduces the number of kick failure. This dramatically improves the stability and power of the shot, and enables stable forward delivery of the ball. As a result, we managed to improve its performance as a "robot that can surely score goals”. The DIGILENT IG22 1/19 motor is used for the drive system to achieve a good balance of controllability and power of the robot. Furthermore, the two-layer omni wheel, which has evolved from a single-layer structure, provides smooth movement. We also focused on making it easy to repair and debug the robot during the game. The on-board OLED Display enables us to check the real-time sensor data for quick troubleshooting and adjustments, eliminating the need for a PC connection and greatly improving the maintenance performance. As a main microcontroller, we chose Teensy 4.0, ensuring high-speed communication and rich I/O expandability. In addition, we have placed emphasis on maintainability and stability through the use of flat cables, LEDs, and wiring design that takes noise suppression into consideration. Also, we used to manufacture the attacker and goalkeeper robot separately. But from this time, both robots share all sensors and circuit boards, simplifying parts management and achieving a high degree of interchangeability.

I2C

# Method / Production / Design

# Munako Aegis

# Soccer LWL

# League

# JAPAN

# Munakata High School

# Team Name

# Our School

# Region

# Abstract

# Maiki Kimura

# Umi Fujita

# Yuta Kurisaki

# Koki Suehiro

# Team Member

Aircraft and Circuit Design Manager

Goalkeeper Program Manager

Attacker Program Manager

# Sponsor

Circuit Design, Media
Manager

# Smoothing Sensor Readings Using Moving Average

There were some fluctuations in the analog values from the ball sensor. To reduce this, we applied a moving average filter to the sensor readings. We rolled the ball away from the sensor and observed the changes in the readings. We analyzed how the variation changed with different numbers of moving average samples and finally chose 10 samples. The graph below compares the results with and without the moving average.
Result：

The graph shows that applying a moving average filter makes the sensor readings smoother. Based on this result, we also applied the moving average to the analog values of the line sensor, not just the ball sensor.

Omnidirectional Mirror

### one-layer structure

### two-layer structure

We are “Munako Aegis,” a team of four Japanese high school students competing in the Lightweight League.
We began our activities in the 2023 season and have been steadily improving our skills through daily, dedicated work on our robot.

When we first started, none of us had any specialized skills. However, we tackled mechanical design, programming, and circuit design every day, gaining knowledge and experience through trial and error. In our first year, we placed first in the preliminary competition and qualified for the Japan Open. However, we finished a disappointing 31st out of 64 teams in the main event.
Nevertheless, we didn't give up and kept working hard. This year, we won first place at the Japan Open. We also won the Best Presentation Award.

We primarily use Autodesk Fusion for mechanical design and KiCad for circuit design. For fabrication, we utilize 3D printers and CNC milling machines to develop robots efficiently and with high precision.
We write programs in Visual Studio Code, using C++ for the microcontroller and Micro Python for camera control, developed with the Open MV IDE.

Our robot uses duralumin for its body to combine light weight with high durability. We made exterior components, such as the battery box and side covers, ourselves using a 3D printer, allowing for design flexibility. For the circuit board, we asked our sponsor, JLCPCB, to fabricate it with high precision to achieve a stable circuit configuration.
The camera system uses an Omnidirectional Mirror, which we made ourselves by heat-pressing vinyl chloride. This allows a single camera to provide a 360-degree field of view while significantly reducing costs. In addition, a kicker mechanism is installed using a solenoid provided by TAKAHA.

To address the “line-out” issue that many teams have struggled with in recent years, we incorporated speed control.
The robot measures its speed in real time as it moves and runs at the optimum speed according to its court position to prevent line-outs at the fastest possible speed.
In addition, we use a double-structured omni wheel design. The double structure increases the ground contact area with the floor and improves braking ability.
Red LEDs are used for the line sensor to improve response speed and accuracy. These innovations strengthen the line area.

For ball detection, we use a multiplexer to handle multiple inputs despite a limited number of pins, and we stabilize noisy values using moving average processing. In addition, an LCD monitor allows the user to check various values in real time without connecting to a PC.

In preparation for the world championships, we reviewed our robot’s design. The shape of the robot, which used to differ between the attacker and the goalkeeper, is now unified. By adopting two identical robots that combine the advantages of both roles, it is now possible to switch roles immediately during a match. Furthermore, all sensors and circuit boards are also standardized, resulting in improved parts
management and even higher compatibility. You can follow our activities on X (formerly Twitter). We also publish all our data on GitHub.

11.1V

### Battery

:Kypon
1300mAh/ 3s /11.1V
Unit price:$13.84

11.1V

Multiplexer
Unit price:$1.34

Digital

Analog

## Main Controller

:Teensy 4.0
Unit price:$42.41

Sub
Controller
:Seeeduino XIAO
Unit price:$6.51

Multiplexer
Unit price:$1.34

Ball sensors
:TSSP58038× 16
Unit price:$1.03

Solenoid
:CB1037 x 1
Unit price:$19.6

Motor
:DIGILENTIG22 1/19
Unit price$14.8

X 4

Motor Driver
DAISEN DSR-1202
IC:VNH2SP30 x 4
・0.3V ~ 16.0V
・15~30A
Unit price:$135.69

Gyro Sensor
:AE-BNO055-BO
Unit price:$3.29

### Kicker System

:XL6009
Unit price:$0.75
11.1V | 48V

5.0V

UART | UART

Digital

I2C

UART

Voltage
Conversion Circuit
Using IC :
OKL-T/6-W12N-C
11.1V to 5.0V
Unit price:$6.03

Analog

Sub
Controller
:Seeeduino XIAO
Unit price:$6.51

Line Sensors
:NJI7502
Unit price:$0.34

Debug System

O-LED Display
：SSD1306
Unit price$3.97

Tactile Switch x 3
Unit price:$0.1

# Robot’s Structure

Vision System

Omnidirectional
Mirror

Camera
:OpenMV H7
Unit price:$80

UART

The motors we used on the robot last season
were 6-volt motors, which limited its speed and performance. So we decided to look for faster and more efficient motors. While keeping costs as low as possible, we chose 12-volt motors. As a result, we selected the following motor options.
・ DC geared motor 12V 1:19（DIGILENT IG22 1/19）
（ about 19 dollars ）June 2024 This motor had the performance we were looking for and
we thought it was a good choice. However, while this motor increased the speed, it caused more out of bounds.
So, even if the robot is fast, it's meaningless if it goes out of bounds.
In the past, the motor speed was reduced to prevent out of bounds,
but there was a problem with the motor continuing to accelerate as it was. To solve this problem, we decided to use the BNO055 to measure the robot‘s speed. This allows us to reduce its speed near the boundary lines to prevent out-of-bounds, while allowing it to reach maximum speed at the center of the court.

Experimental environment
For the Verification 1 and Verification 2 experiments, we ran the robot from one end of the court to the other and used a recording timer to measure the distance traveled every 0.1 second. Based on these measurements, we calculated the average speed for each 0.1-second interval and created a graph showing how the speed changed over time. （See Photos 1 and 2）

Speed control
Determine the set speed. If the measured speed is below the set speed, increase the motor power. Conversely, if the speed exceeds the set speed, decrease the motor power. This method is called "speed control."（See Figure 1）We conducted the following verification to evaluate whether
this method is effective in preventing out of bounds.

Verification 1:
Exploring the difference between speed control and no control. To verify that the speed control was functioning correctly, we conducted experiments both with and without speed control.
Next, we compared the relationship between velocity (v: cm/s) and time (t: seconds) using graphs. Result：

The graph shows that the speed is constant at 80 cm/s with speed control compared to without.

Verification 2: Effect of Speed Control on Deceleration Behavior
The graph compares the relationship between velocity (v: cm/s) and time (t: seconds) in two cases. In the first case, the robot was accelerated to a set speed using speed control, and then decelerated by reducing that set speed. In the second case, the robot was operated without speed control at a fixed PWM value for a certain time, and then decelerated by reducing the PWM value.
Result：

The graph shows a case where the final speeds after deceleration are approximately equal with and without speed control. In this example, the time required to decelerate to the set speed is shorter with speed control than without it, even though the initial speed was higher with speed control.
This indicates that speed control is more effective for deceleration. (See Graph 2)

Verification 3: Find the maximum value of the speed that is not out of bounds
The goal was to find the maximum speed at which the robot could stop without going out of bounds and hitting a wall when stepping on the line. We created a program to brake when stepping on the line, varied the set speed, and recorded the maximum speed that did not go out of bounds.

The results show that a set speed of 600 is the maximum optimal speed at which the robot can stop without going out of bounds. Therefore, this speed was set as the maximum speed when near the line. In other areas , we decided to use speed control with no upper speed limit.
(See Table 1)
For position estimation, a camera is used to estimate the position of the robot based on the direction of the center of the court.

Conclusion：
From Verification 1, it was observed that without speed control, the robot’s speed continues to increase, whereas with speed control, the speed eventually stabilizes.
From Verification 2, it was shown that the motor with speed control decelerates more quickly than the one without it.From Verification 3, the maximum speed at which the robot can stop without going out of bounds was identified. Previously, this speed had been manually adjusted through trial and error.

## Comparison of Speeds Without Going Out of Bounds

▷Photo１ The experiment scene | ▷Photo２ The experiment scene

# Speed control that leads to improved line control

▷Fig2

# Data / Results / Discussion

### Verification1

### Verification2

### Verification3

### Speed instability

Slow deceleration | Quick deceleration Speed stability
Unclear maximum speed | Clear maximum speed

## As a result of this test, the following is now possible

## Set speed

### Fast

### Slow

▷Fig1 Mechanism of speed control

▷Gragh2

▷Gragh1

## Effect of Speed Control on Deceleration

## Effect of Speed Control on Velocity Stability

Effect of a Moving Average Filter | ▷Gragh3
stand-alone camera | Omnidirectional camera

Before introduction
Of multiplexer

After introduction
Of multiplexer

Wired to curve

Old capture zone | New capture zone

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
0 | 0.5 | 1 | 1.5 | 2 | 2.5
| with speed control
| without speed control

(v: cm/s)

(t: seconds)

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
0 | 0.5 | 1 | 1.5 | 2 | 2.5
| with speed control
| without speed control

(v: cm/s)

(t: seconds)

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
without the moving average filter

with the moving average filter

Analog value

Number of readings

# Evaluation of Optimal LED Color for Line Sensors

Our line sensors have been using white LEDs until now, We decided to experiment with the question of whether white LEDs are really suitable. We are using full-color LEDs in the experiment that can change the color and brightness of the light. We made a graph and a table of the data when the robot passed a white line using red, green, and blue light compared to the white light we had used before.

Looking at Figure 4, it’s easy to assume that white light is advantageous because the response values are high. However, it’s also evident that the values when there is no response are higher compared to those of other colors.
For line sensors, a greater difference between the minimum and maximum values is more advantageous. Comparing the differences in Figure 5, red and blue show a larger range than the other two colors. However, blue is a prohibited color and cannot be used. Therefore, it can be concluded that the most suitable light source for the sensor is red.
Response Values by Color | Max-Min Difference for Each Color
▷Gragh4 | ▷Gragh5

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
white

red

green

blue

0 | 100 | 200 | 300

blue

green

red

white

# 今田 耕司様

# Team Activities

・KiCad
Used for circuit
fabrication

Our team mainly uses the following software.

・ GitHub
Used for data
storage

・ Visual Studio
Used for programming
(except for the camera)
with C++

## Design

・Autodesk Fusion
Used for designing
the robot’s frame and
components

## Program

・ OpenMV IDE
Used for programming
the camera with Python

・ Discord
Used for sharing
information among team
members

## Management

# Tool

0

20000

40000

60000

80000

100000

120000

140000

160000

180000

200000

# Robot effort min

Our team has been participating in the RoboCup Soccer Lightweight League since last season. This is now our second year. The team consists of four members — three of whom have been involved in robot competitions since high school, and one since junior high school. Despite being a relatively new team, we have set a major goal of "winning the world championship," and we’ve been working hard every day to build our robots and improve our technical skills. Given our limited time, we established a clear activity policy to ensure that every team member could grow steadily. In this presentation, we would like to introduce the policies we followed and how we advanced our activities based on them.

Each team
member built
their own robot,
deepening their
understanding of
its structure and
mechanisms.

Through the process
of building robots,
we identified our
own strengths and
weaknesses and
assigned team roles
accordingly.

## Year 1 - H2

Reflecting on our experience at the Japan Open, we discussed the mechanisms we wanted to implement, examined the
necessary technologies, created a plan, and clarified each step to steadily improve our technical skills.
Year 2 - H1 | Year 2 - H2 | Worlds Prep

## Winning the World Championship

Based on our past match
experiences, we discussed
additional mechanisms and
strategies we wanted to
implement, and as a team, we talked about what preparations were necessary for the upcoming competition.

## Final Goal

Based on our
experience at the
Japan Open, we
discussed what we
need to do to adapt to
the environment of the
World Championship.

# Ⅾaily accumulation and planning are important

In order to enhance our technical skills, we have dedicated an enormous amount of time and made continuous, extraordinary efforts. On weekends, we work from 9 a.m. to 5 p.m., and on weekdays, we usually continue activities from 4 p.m. to 7 p.m. after school. The graph on the right shows the cumulative number of hours we’ve spent on robot development, broken down by month. The vertical axis represents the time spent working on the robot (in minutes), and the horizontal axis represents the progression of dates. This graph is a record of our relentless efforts to aim for the world stage, despite having limited time.

Our total activity time amounts to approximately 180,000 minutes — or about 3,140 hours.

This massive amount of time is proof of our wholehearted belief that “small efforts every day will eventually lead to great achievements. ”Through our journey, we have not only built robots — we’ve also developed the very ability to persevere as a team. Because we experienced both failure and success with our own hands, we’ve come to truly understand that continued effort leads to growth and results — and ultimately to building stronger robots.

Last season's frame This season's frame

## Year 1 - H1

New line sensor layout

Actual screen

## 01 Line Sensor

This season‘s robot is equipped with a more advanced line detection system that combines a circular line sensor with the outer line sensors. First, the line sensor is equipped with more LEDs than before. This allows the robot to accurately detect white lines over a wider area, in the outer areas. Seeduino XIAO is used to read the sensors, but initially the number of sensors that could be installed was limited due to the limited number of ports. The number of sensors could be increased by introducing a multiplexer. This sensor system has been particularly effective on the goalkeeper robot. This system makes it possible to track the white line
precisely and maintain stable operation at all times during play.
The circular line sensor plays an important role in determining
the direction of course. By reliably detecting them, the robot can always maintain the correct trajectory. Meanwhile the outer line sensors serve as a reference to correct the robot so that it does not deviate from the course. Furthermore, the robot used in the national competition had several occasions where It went out of the white line on the field. Therefore, by reviewing the placement of the line sensors, we succeeded in reducing the “unresponsive blind spots” that existed at the bottom of
the robot. This has further improved the overall line detection
accuracy, as well as the consistency and accuracy of operation.
We previously used optical modulation photo ICs, which cost 250 yen each. However, to reduce costs, we introduced phototransistors, which cost 50 yen each.

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

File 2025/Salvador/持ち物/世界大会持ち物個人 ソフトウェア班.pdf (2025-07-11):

ロボット部品 | | スパイクカバー | 2 | | 道具 | その他
| 名前 | 個数 | チェック | | ドリブラー | 2 | 配線 | カシメ機 | 2 | | バッテリー充電器 | 4
板 | 上板 | 2 | | | 筒固定 | 4 | | ワイヤーストリッパー | | | 充電中看板 | 2
| 下板 | 2 | | | コンデンサー固定 | 4 | 固定 | ビニールテープ黒 | 2 | | ボール | 4
オムニホイール | ノーマル | 8 | | | IR固定 | 8 | | ビニールテープ白 | | | お土産x15 | 2
| 小さめ | 8 | | | ミラー固定 | 1 | | 養生テープ | 2 | | ちりとり（末） | 1
| デュアル | 8 | | | スペーサー後ろ | 4 | | 両面テープ | 2 | | マーカーペン | 2
| スパイク | 8 | | POM | ラインカバー | | | ライン用テープ(栗） | 1 | | はかり（末） | 1
モーター | Digilent IG22 | 12 | | | オムニinside | | | 結束バンド | 2 | | 延長ケーブル | 2
| ブラシレスモーター | 2 | | | タイヤカバー | | 接着 | 瞬間接着剤 | 2 | | ポスター | 2
キッカー | ソレノイド | 3 | | ジュラルミン | IR固定 | | | はがし液 | 1
マイコン | Teensy4.0 | 4 | | | ハンドル | | | グルーガン | 2
| Seeeduino xiao | 8 | | その他 | トップマーカー | | | グルーティック白、黒 | 2
| Open MV | 3 | | | | | その他 | ユニバーサルプレート | 2
| 4ch MD | 3 | | | | | | ユニバーサルピラー
| トワイライト | 3 | | | | | | 予備の乾電池単四ⅹ3 | 2
| BNO055　青 | 3 | | | | | | 予備の乾電池9V | 2
| BNO055　緑 | 3 | | | | | | アルミ複合版 | 2
| L3GD20H | 3 | | | | | | 透明ファイル | 2 | 追加
| ESC | 3 | | | | | | エアダスター（栗） | 1
3Dプリンター | サイドカバー | 4 | | | | | | タップと刃（栗） | 1
| サイドカバー書き込み側 | 4 | | | | | | 黒ファイル | 2
| バッテリーケース | 2 | | | | | | ドライバーbox（栗） | 1
| モーター固定具 | 12 | | | | | | 精密ドライバーセット（栗） | 1
| ボール捕捉エリア | 3
| ハンドルミラー固定 | 3
| IRカバー | 3
| オムニinside | 8

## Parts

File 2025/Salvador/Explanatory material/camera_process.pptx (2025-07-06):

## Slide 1

camera

回路

写真

Hardware

5.0V

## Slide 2

Software

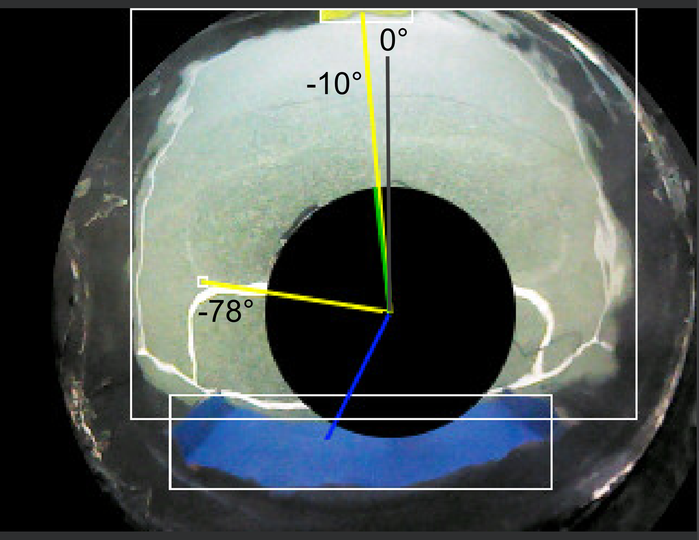
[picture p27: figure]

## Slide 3

Software

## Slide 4

Software

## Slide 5

Software

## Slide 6

Software

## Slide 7

Software

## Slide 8

Software

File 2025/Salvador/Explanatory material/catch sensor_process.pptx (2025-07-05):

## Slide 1

Catch sensor

回路

Hardware

写真

5.0V

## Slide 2

Software

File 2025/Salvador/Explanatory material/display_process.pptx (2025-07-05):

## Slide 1

Display

回路

写真

Hardware

5.0V

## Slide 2

Software

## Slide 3

Software

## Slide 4

Software

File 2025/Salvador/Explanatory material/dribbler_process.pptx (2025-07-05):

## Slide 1

Dribbler

回路

写真

Hardware

5.0V

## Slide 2

Software

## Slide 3

Software

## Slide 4

Software

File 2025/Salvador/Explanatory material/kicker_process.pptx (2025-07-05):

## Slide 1

kicker

回路

写真

Hardware

5.0V

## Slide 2

Software

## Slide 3

Software

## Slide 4

Software

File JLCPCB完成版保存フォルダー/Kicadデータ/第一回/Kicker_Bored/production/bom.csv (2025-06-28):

Designator | Footprint | Quantity | Value | LCSC Part #
C1, C2 | JST_XH_B2B-XH-A_1x02_P2.50mm_Vertical | 2 | C
J1 | JST_VH_B2P-VH_1x02_P3.96mm_Vertical | 1 | Conn_01x02_Socket
J3 | JST_XH_B3B-XH-A_1x03_P2.50mm_Vertical | 1 | Conn_01x03_Socket
J4 | JST_XH_B2B-XH-A_1x02_P2.50mm_Vertical | 1 | Conn_01x02_Socket
Q1 | K15A20D | 1 | PMOS
Q3 | K15A20D | 1 | NMOS
R1, R3, R8 | 0805 | 3 | 330K
R2, R9 | 0805 | 2 | 1K
R4 | 0805 | 1 | 10K
R6, R7 | 0805 | 2 | 2K
U1, U2 | DIP-4_W7.62mm | 2 | EL817

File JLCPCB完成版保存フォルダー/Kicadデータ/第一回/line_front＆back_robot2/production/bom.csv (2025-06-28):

Designator | Footprint | Quantity | Value | LCSC Part #
D1, D2, D3, D5 | LED_WS2812B-2020_PLCC4_2.0x2.0mm | 4 | NeoPixel_THT
J2 | PinHeader_1x04_P2.54mm_Horizontal | 1 | Conn_01x04_Pin
J3 | PinHeader_1x01_P2.54mm_Vertical | 1 | Conn_01x01_Pin
Q1, Q10, Q2, Q3, Q4, Q7, Q8, Q9 | LED_D3.0mm_Clear | 8 | Q_Photo_NPN
R8 | 2010 | 1 | 1K
RV2 | Potentiometer_Vishay_TS53YJ_Vertical | 1 | R_Potentiometer_Trim_US

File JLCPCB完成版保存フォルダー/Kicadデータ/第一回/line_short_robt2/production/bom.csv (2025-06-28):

Designator | Footprint | Quantity | Value | LCSC Part #
D1 | LED_WS2812B-2020_PLCC4_2.0x2.0mm | 1 | NeoPixel_THT
J1 | PinHeader_1x04_P2.54mm_Horizontal | 1 | Conn_01x04_Pin
J2 | PinHeader_1x01_P2.54mm_Vertical | 1 | Conn_01x01_Pin
Q1, Q2 | LED_D3.0mm_Clear | 2 | Q_Photo_NPN
R1 | 2010 | 1 | 1K
RV1 | Potentiometer_Vishay_TS53YJ_Vertical | 1 | R_Potentiometer_Trim_US

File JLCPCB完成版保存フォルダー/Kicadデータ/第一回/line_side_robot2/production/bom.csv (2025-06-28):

Designator | Footprint | Quantity | Value | LCSC Part #
D1, D2, D3, D4_2, D4, D5, D6 | LED_WS2812B-2020_PLCC4_2.0x2.0mm | 7 | NeoPixel_THT
J1 | PinHeader_1x04_P2.54mm_Horizontal | 1 | Conn_01x04_Pin
J2 | PinHeader_1x01_P2.54mm_Vertical | 1 | Conn_01x01_Pin
Q1, Q10, Q11, Q12, Q13, Q14, Q2, Q3, Q4, Q5, Q6, Q7, Q8, Q9 | LED_D3.0mm_Clear | 14 | Q_Photo_NPN
R1 | 2010 | 1 | 1K
RV1 | Potentiometer_Vishay_TS53YJ_Vertical | 1 | R_Potentiometer_Trim_US

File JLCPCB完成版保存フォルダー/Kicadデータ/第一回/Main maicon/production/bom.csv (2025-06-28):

Designator | Footprint | Quantity | Value | LCSC Part #
BACK, RV1, RV2 | Variable_Register | 3 | R_Potentiometer_Trim_US
BNO1 | BNO00 | 1 | ~
C1, C2 | C_Radial_D6.3mm_H5.0mm_P2.50mm | 2 | C
D1 | LED_D3.0mm_Clear | 1 | LED
D2, D3, D4, D5, D6, D7 | LED_WS2812B-2020_PLCC4_2.0x2.0mm | 6 | NeoPixel_THT
J1 | JST_XH_B2B-XH-A_1x02_P2.50mm_Vertical | 1 | 12V_IN
J2, J3 | JST_XH_B4B-XH-A_1x04_P2.50mm_Vertical | 2 | MD
J4, J9 | JST_XH_B4B-XH-A_1x04_P2.50mm_Vertical | 2 | Conn_01x04_Pin
J5, J7 | JST_XH_B3B-XH-A_1x03_P2.50mm_Vertical | 2 | Conn_01x03_Pin
J6 | JST_XH_B5B-XH-A_1x05_P2.50mm_Vertical | 1 | Conn_01x05_Pin
J8 | IDC-Header_2x07_P2.54mm_Vertical | 1 | Conn_02x07_Top_Bottom
L3GD20H1 | L3GD20OH | 1 | ~
R1, R2, R3 | R_Axial_DIN0204_L3.6mm_D1.6mm_P5.08mm_Vertical | 3 | R
SW1, SW2, SW3 | PinSocket_1x03_P2.54mm_Vertical | 3 | SW_DPST_x2
SW4 | SW_PUSH_6mm_H5mm | 1 | SW_Push
U1 | Teensy40 | 1 | Teensy4.0
U2 | seeeduinoXIAO | 1 | SeeeduinoXIAO

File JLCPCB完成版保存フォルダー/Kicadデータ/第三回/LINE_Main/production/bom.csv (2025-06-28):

Designator | Footprint | Quantity | Value | LCSC Part #
C1, C2 | PinHeader_1x02_P2.54mm_Vertical | 2 | C
D1, D10, D11, D12, D13, D14, D15, D16, D17, D18, D19, D2, D20, D21, D22, D23, D24, D25, D26, D27, D28, D29, D3, D30, D31, D32, D4, D5, D6, D7, D8, D9 | LED_D3.0mm_Clear | 32 | LED
J1 | JST_XH_S4B-XH-A_1x04_P2.50mm_Horizontal | 1 | Conn_01x04_Socket
J2, J3, J4 | PinHeader_1x04_P2.54mm_Vertical | 3 | Conn_01x04_Socket
Q1, Q10, Q11, Q12, Q13, Q14, Q15, Q16, Q17, Q18, Q19, Q2, Q20, Q21, Q22, Q23, Q24, Q25, Q26, Q27, Q28, Q29, Q3, Q30, Q31, Q32, Q4, Q5, Q6, Q7, Q8, Q9 | LED_D3.0mm_Clear | 32 | Q_Photo_NPN
R1, R10, R11, R12, R13, R14, R15, R16, R17, R18, R19, R2, R20, R21, R22, R23, R24, R25, R26, R27, R28, R29, R3, R30, R31, R32, R33, R34, R35, R36, R37, R38, R39, R4, R40, R41, R42, R43, R44, R45, R46, R47, R48, R5, R6, R7, R8, R9 | 0805 | 48 | R
RV1, RV10, RV11, RV12, RV13, RV14, RV15, RV16, RV2, RV3, RV4, RV5, RV6, RV7, RV8, RV9 | Potentiometer_Vishay_TS53YJ_Vertical | 16 | R_Potentiometer_Trim_US
U1 | SSOP-24_5.3x8.2mm_P0.65mm | 1 | CD74HC4067SM
U2 | seeeduinoXIAO | 1 | Seeeduino_Xiao

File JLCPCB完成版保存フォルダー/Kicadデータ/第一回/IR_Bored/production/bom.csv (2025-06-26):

Designator | Footprint | Quantity | Value | LCSC Part #
C1, C10, C11, C12, C13, C14, C15, C16, C2, C3, C4, C5, C6, C7, C8, C9 | 0402 | 16 | 104
CAMERA_RST | SW_PUSH_6mm_H5mm | 1 | SW_DIP_x01
J1 | PinHeader_1x04_P2.54mm_Vertical | 1 | Conn_01x04_Socket
J2, J3 | JST_XH_B4B-XH-A_1x04_P2.50mm_Vertical | 2 | Conn_01x04_Pin
J4 | PinHeader_2x11_P2.54mm_Vertical | 1 | Conn_02x11_Odd_Even
R1, R10, R11, R12, R13, R14, R15, R16, R2, R3, R4, R5, R6, R7, R8, R9 | 0805 | 16 | 22k
SW1, SW2, SW3 | SW_PUSH_6mm_H5mm | 3 | LCD
SW5 | PinHeader_1x02_P2.54mm_Vertical | 1 | SW_DIP_x01
U1, U10, U11, U12, U13, U14, U15, U17, U2, U3, U4, U5, U6, U7, U8, U9 | Vishay_MINICAST-3Pin | 16 | TSSP58P38
U16 | SSOP-24_5.3x8.2mm_P0.65mm | 1 | CD74HC4067SM

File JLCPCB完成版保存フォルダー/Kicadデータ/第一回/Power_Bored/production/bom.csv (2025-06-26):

Designator | Footprint | Quantity | Value | LCSC Part #
BT1 | JST_VH_B2P-VH_1x02_P3.96mm_Vertical | 1 | Battery
C2, C3 | C_Disc_D3.8mm_W2.6mm_P2.50mm | 2 | C
D1, D2 | D_DO-15_P10.16mm_Horizontal | 2 | D
F1 | fuse_socket | 1 | Fuse
J1, J2 | JST_XH_B3B-XH-A_1x03_P2.50mm_Vertical | 2 | Conn_01x03_Socket
J3 | JST_VH_B2P-VH_1x02_P3.96mm_Vertical | 1 | Conn_01x02_Socket
J4, J5 | JST_XH_B2B-XH-A_1x02_P2.50mm_Vertical | 2 | Conn_01x02_Socket
MES1 | voltage_counter | 1 | Voltmeter_DC
R1, R2 | R_Axial_DIN0204_L3.6mm_D1.6mm_P5.08mm_Horizontal | 2 | R
RV1 | Potentiometer_Bourns_3296W_Vertical | 1 | R_Potentiometer_Trim_US
SW1 | DS-850k | 1 | SW_DIP_x01
SW2 | JST_XH_B3B-XH-A_1x03_P2.50mm_Vertical | 1 | SW_DIP_x01
U1 | DCDC-murata-6A | 1 | OKL-T_6-W12N-C
U2 | XL6009 | 1 | ~

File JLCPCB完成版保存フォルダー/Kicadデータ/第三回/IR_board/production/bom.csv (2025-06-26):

Designator | Footprint | Quantity | Value | LCSC Part #
C1, C10, C11, C12, C13, C14, C15, C16, C2, C3, C4, C5, C6, C7, C8, C9 | C_Disc_D5.0mm_W2.5mm_P2.50mm | 16 | 104
Camera_RST1 | SW_PUSH_6mm_H5mm | 1 | SW_DIP_x01
J1 | PinHeader_1x04_P2.54mm_Vertical | 1 | Conn_01x04_Socket
J2 | IDC-Header_2x07_P2.54mm_Vertical | 1 | Conn_02x07_Top_Bottom
R1, R10, R11, R12, R13, R14, R15, R16, R2, R3, R4, R5, R6, R7, R8, R9 | R_Axial_DIN0204_L3.6mm_D1.6mm_P5.08mm_Vertical | 16 | 22k
SW1, SW2, SW3 | SW_PUSH_6mm_H5mm | 3 | LCD
SW4 | PinHeader_1x02_P2.54mm_Vertical | 1 | SW_DIP_x01
U1 | seeeduinoXIAO | 1 | SeeeduinoXIAO
U10, U11, U12, U13, U14, U15, U16, U17, U2, U3, U4, U5, U6, U7, U8, U9 | PinHeader_1x03_P2.54mm_Vertical | 16 | TSSP58038
U18 | SSOP-24_5.3x8.2mm_P0.65mm | 1 | CD74HC4067SM
U19 | OpenMV | 1 | open_mv

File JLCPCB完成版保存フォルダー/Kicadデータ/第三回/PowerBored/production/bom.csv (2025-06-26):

Designator | Footprint | Quantity | Value | LCSC Part #
106, C1 | C_Disc_D3.8mm_W2.6mm_P2.50mm | 2 | C
12V_2, 12V, FET | JST_XH_S3B-XH-A_1x03_P2.50mm_Horizontal | 3 | Conn_01x03_Socket
5V_2, 5V | JST_XH_S2B-XH-A_1x02_P2.50mm_Horizontal | 2 | Conn_01x02_Socket
BT1 | JST_VH_B2P-VH_1x02_P3.96mm_Vertical | 1 | Battery
C3, C4 | JST_XH_B2B-XH-A_1x02_P2.50mm_Vertical | 2 | C
D1, D2 | D_DO-15_P10.16mm_Horizontal | 2 | D
FUSE | fuse_socket | 1 | Fuse
MES1 | voltage_counter | 1 | Voltmeter_DC
Q1 | K15A20D | 1 | PMOS
Q2 | K15A20D | 1 | NMOS
R1, R2 | R_Axial_DIN0204_L3.6mm_D1.6mm_P5.08mm_Horizontal | 2 | R
R10, R6 | 0805 | 2 | 1K
R3, R4, R7 | 0805 | 3 | 330
R5, R9 | 0805 | 2 | 2K
R8 | 0805 | 1 | 10K
RV1 | Potentiometer_Bourns_3296W_Vertical | 1 | R_Potentiometer_Trim_US
SELNOID | JST_XH_B2B-XH-A_1x02_P2.50mm_Vertical | 1 | Conn_01x02_Socket
SWITCH_2 | JST_XH_B3B-XH-A_1x03_P2.50mm_Vertical | 1 | SW_DIP_x01
SWITCH | DS-850k | 1 | SW_DIP_x01
U1 | DCDC-murata-6A | 1 | OKL-T_6-W12N-C
U2 | XL6009 | 1 | ~
U3, U4 | DIP-4_W7.62mm | 2 | EL817
VOLTAGE_CHECK | JST_VH_B2P-VH_1x02_P3.96mm_Vertical | 1 | Conn_01x02_Socket

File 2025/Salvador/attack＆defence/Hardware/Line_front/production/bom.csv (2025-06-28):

Designator | Footprint | Quantity | Value | LCSC Part #
D1, D2_2, D2, D3, D4, D7 | LED_D3.0mm_Clear | 6 | LED
J3 | PinHeader_1x04_P2.54mm_Vertical | 1 | Conn_01x04_Socket
Q1, Q15, Q16, Q17, Q3, Q4 | LED_D3.0mm_Clear | 6 | Q_Photo_NPN
R1_2, R1, R2, R4, R5, R6, R7 | 0805 | 7 | R
RV2 | Potentiometer_Vishay_TS53YJ_Vertical | 1 | R_Potentiometer_Trim_US

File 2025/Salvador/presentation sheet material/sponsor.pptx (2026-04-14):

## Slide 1

スポンサー

資金支援

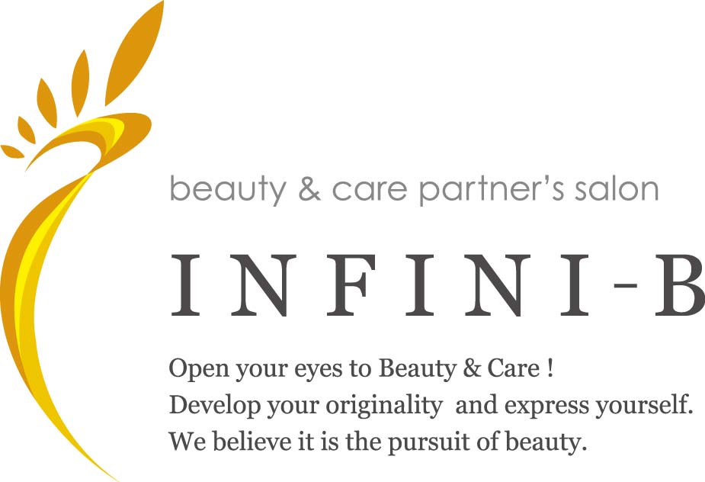
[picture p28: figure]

技術支援

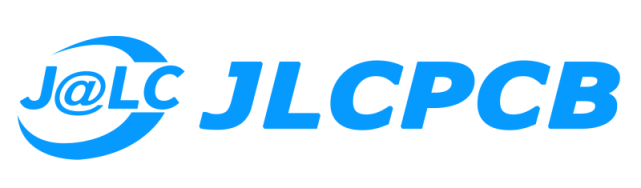
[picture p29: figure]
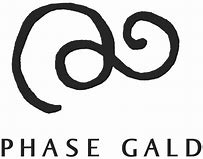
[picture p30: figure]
OIP.fqX9CVUqJgZATrEDRZgoQQHaFz (203×159)
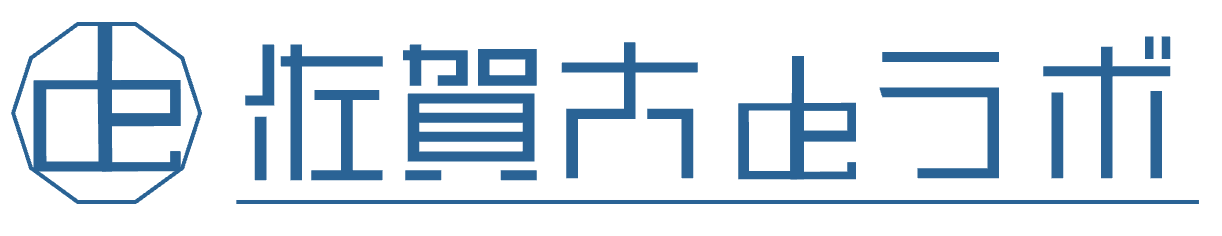
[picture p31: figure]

企業募集
してます！！

福岡県立宗像高等学校電気物理部　　　　TEL:0940-36-2019

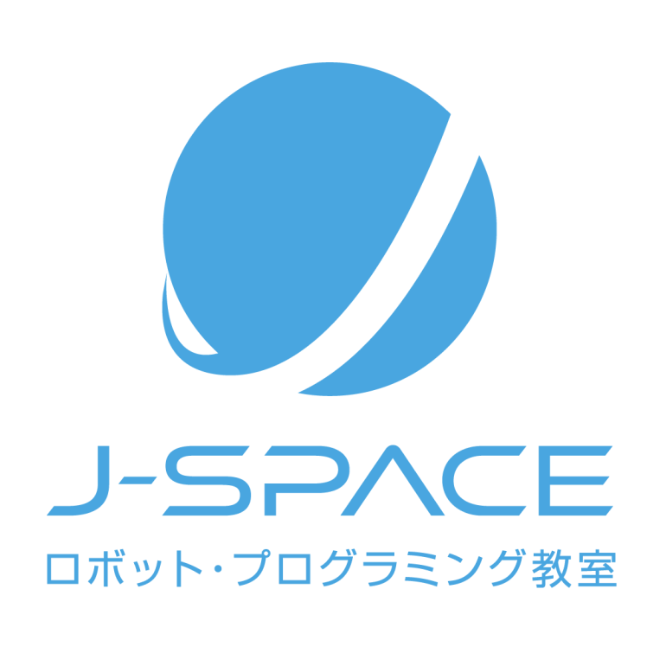
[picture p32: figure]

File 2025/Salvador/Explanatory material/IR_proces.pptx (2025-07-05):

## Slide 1

IR

Hardware

写真

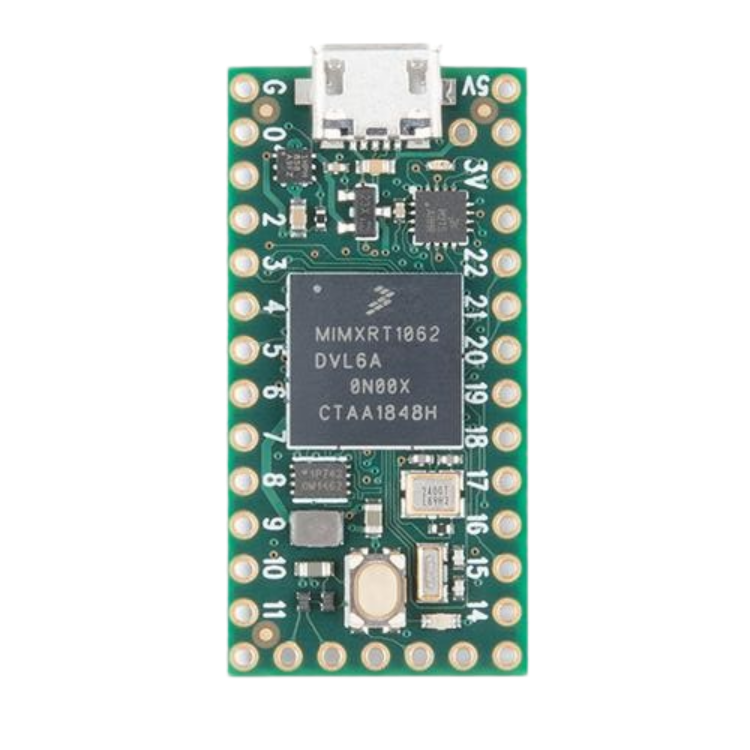
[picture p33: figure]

Main microcontroller・Teensy4.0

回路

Serial

Sub microcontroller
・Seeeduino Xiao

Multiplexer
・HP4067

Ball sensor
・TSSP58038

5.0V

Analog

Analog

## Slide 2

Software

Last Season

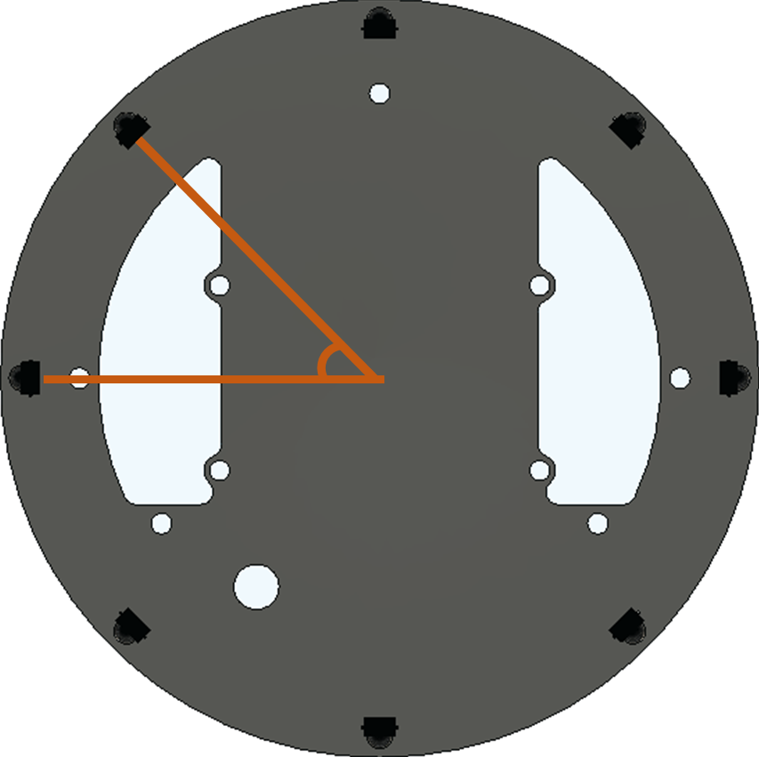
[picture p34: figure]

私たちは、ボールセンサを8個、円形に等間隔で配置しました。
しかし、赤外線ボールの位置によってボールセンサのアナログ値が
変化するため、誤差が生じていました。

This Season


センサの数を16個に増やし、間隔を狭めました。

そこで、この誤差を
減らすために、

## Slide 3

Software

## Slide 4

Software

このブレを減らすために、ボールセンサのアナログ値に対して移動平均を求めることにしました。

区間数を10に設定した場合と、
移動平均を使用しない場合で結果を比較しました。

検証方法としては、ボールセンサから素早くボールを遠ざけ、その値の変化を調べました。

robot

ball

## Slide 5

Software


移動平均とは、一定の期間のデータの平均を取り、時間の経過とともにこの平均を順次更新していきます。

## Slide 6

Software


グラフを見ると、移動平均を使うことで、
値が明らかに滑らかになったことがわかりました。
この結果から、この移動平均をボールセンサに使用しています。

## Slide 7

Software


①

②

③

←最初にfalseにする

①移動平均の標本数

②カウント

③データの保存配列

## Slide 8

Software


①Stock_rotation_numberがstock_rotation_term（標本数）を上回ったら
＝ stock_dataのすべての場所に要素が入る
・ stock_rotation_numbeを0に戻す
・aveをtrueに変える

②stock_dataのstock_rotation_numberの数番目にdataを保存

①

③

②


stock_data

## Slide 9

Software


①

②

←数を一増やす

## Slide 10

Software


現在保存されているもののみで平均をとる

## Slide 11

Software


①


保存されているものすべてで平均をとる

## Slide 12

Software


for文で各センサの値を比べ一番反応しているセンサを見つけます。そして、そのセンサとその両隣のセンサのアナログ値を、それぞれX成分とY成分に分解し、成分ごとに加算し、atan2という関数を使いボールの角度を算出します。

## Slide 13

Software


また、加算後のX成分とY成分を用いて、三平方の定理により距離を算出します。
また、角度と距離をSeeeduino XIAOからTeensy 4.0へシリアル通信により送信します。

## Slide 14

Software

マルチプレクサのアナログ読み込み関数


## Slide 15

Software


ピン番号を配列に保存

初期値

角度計算に使用

0の隣の15,14も保存

15の隣の0,1も保存

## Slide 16

Software

一番反応しているアナログピンを見つける


IR_val…iピンのアナログ値

No1_val…IR_No1ピンのアナログ値

IR_No1…一番反応しているアナログピンの番号

IR_valとNo1_valを比べIR_valの値が低ければ
= IR_No1ピンよりiピンのほうがボールに近い
・No1_val に IR_val を保存
・IR_No1 に iを保存

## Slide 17

Software


No1_valが950より大きい
=ボールが見えてない
・IR_dir = 500(角度を500)
・IR_dis = 500(距離を500)
それ以外
＝ボールが見えている

もしIR_No1 = 1のとき
=1ピンが一番反応している

配列の要素

IR_minu2

IR_minu1

IR_pra1

IR_pra2

IR_No1 += 2

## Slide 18

Software


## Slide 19

Software


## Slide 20

Software

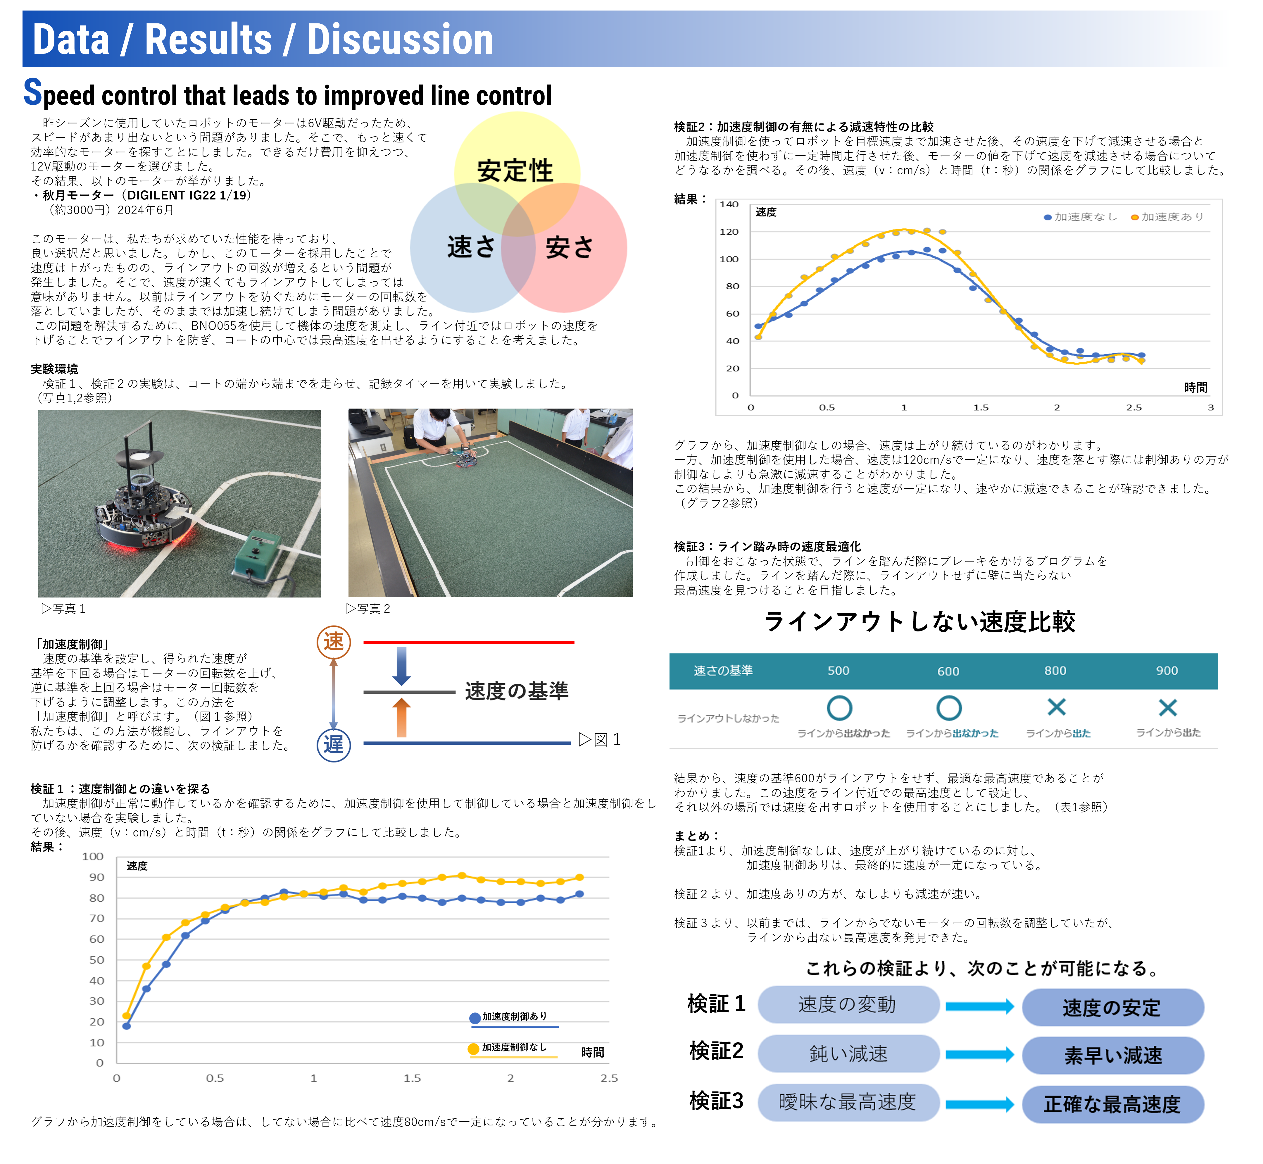
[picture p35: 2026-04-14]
2025/Salvador/presentation sheet material/speedpng.png

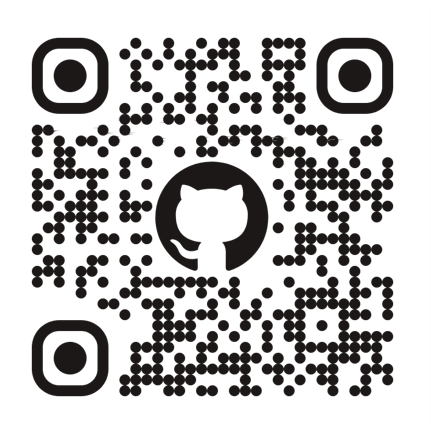
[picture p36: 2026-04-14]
2025/Salvador/presentation sheet material/画像1.png

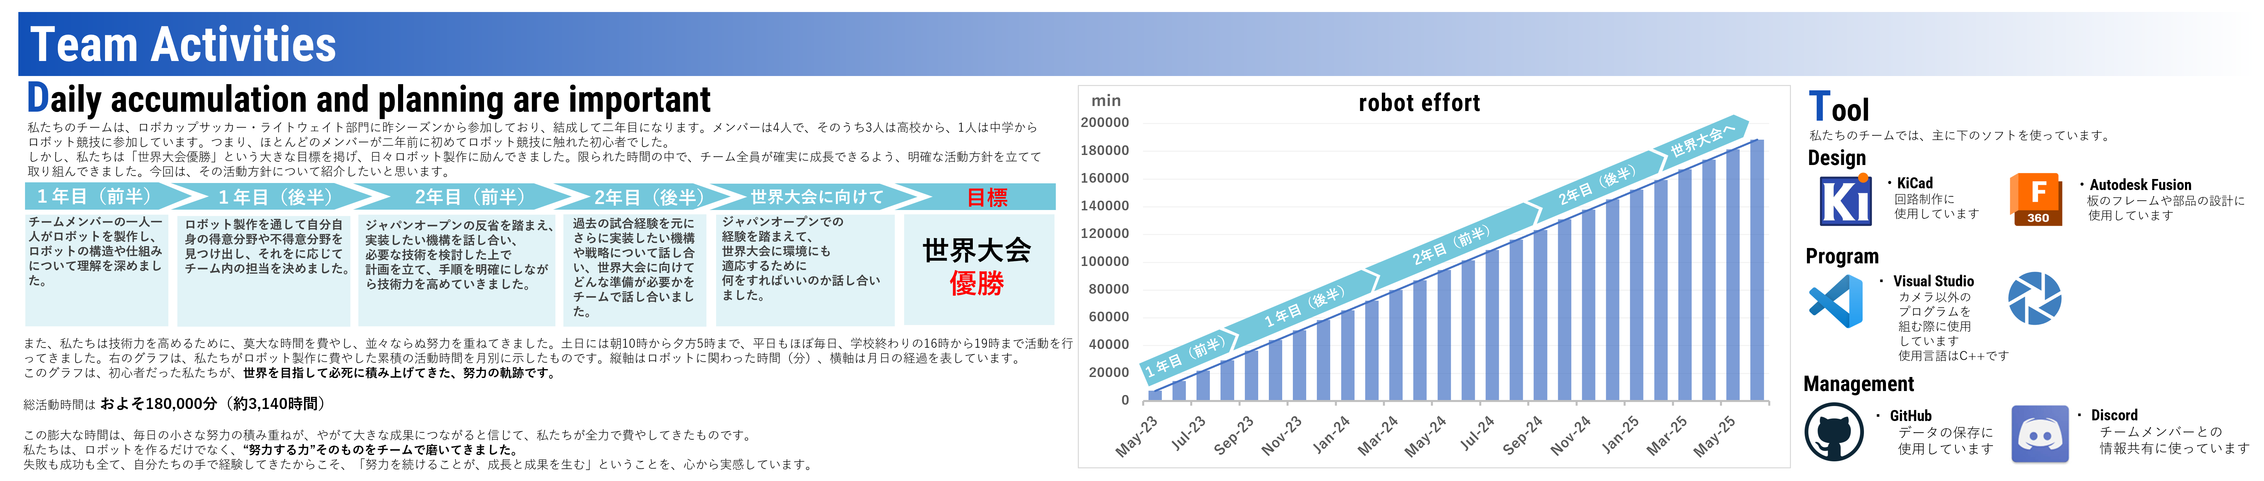
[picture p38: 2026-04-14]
2025/Salvador/presentation sheet material/our teampng.png

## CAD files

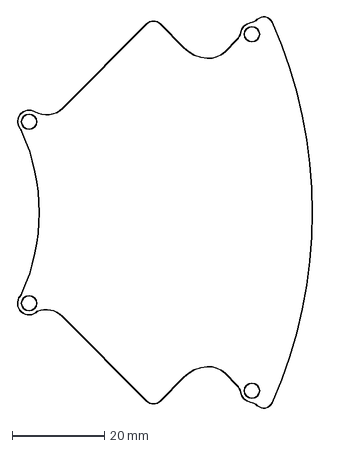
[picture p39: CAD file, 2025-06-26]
JLCPCB完成版保存フォルダー/Kicadデータ/第一回/Main maicon/Main_maicon.dxf
67.3 x 85.2 mm

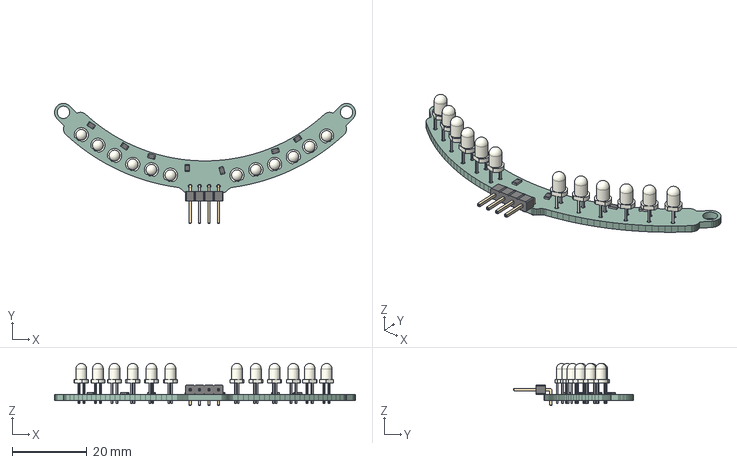
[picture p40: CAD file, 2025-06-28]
2025/Salvador/attack＆defence/Hardware/Line_front/Line_front.step
80.7 x 32.2 x 11.3 mm
Line_front PCB

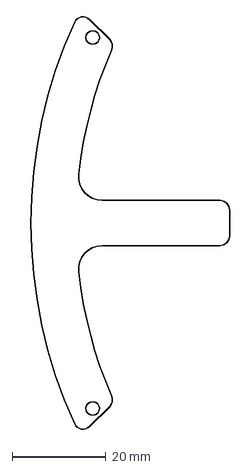
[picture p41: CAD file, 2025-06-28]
2025/Salvador/attack＆defence/Hardware/Line_side&back/Line_side.dxf
45.4 x 88.0 mm

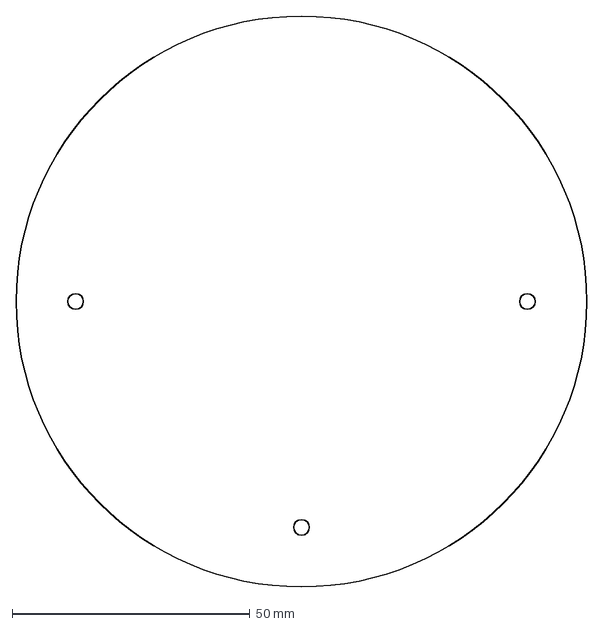
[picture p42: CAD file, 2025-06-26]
JLCPCB完成版保存フォルダー/Kicadデータ/第一回/Camera_Bored/IR_Bored_UNDERSIDE.dxf
120.0 x 120.0 mm

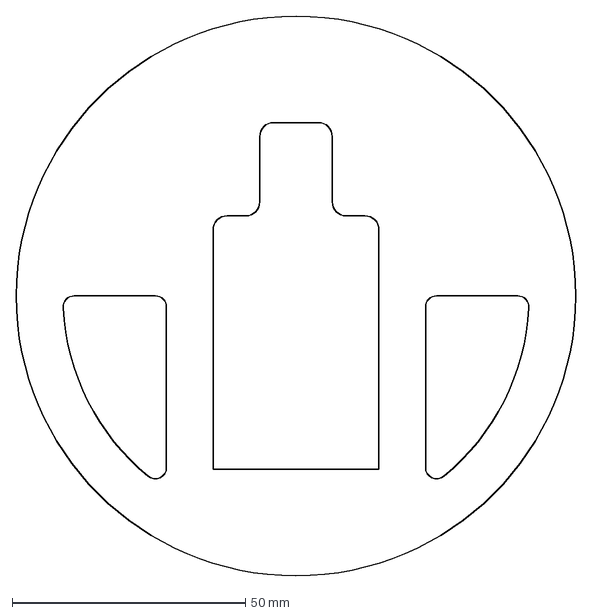
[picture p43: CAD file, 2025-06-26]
JLCPCB完成版保存フォルダー/Kicadデータ/第一回/IR_Bored/IR_Bored_under.dxf
120.0 x 120.0 mm

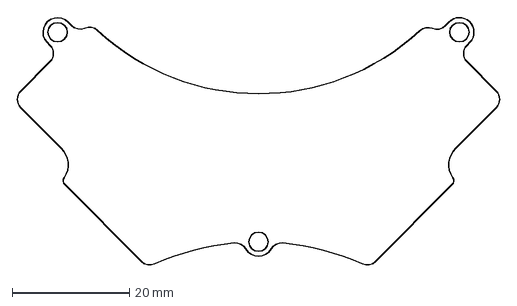
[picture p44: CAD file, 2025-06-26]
JLCPCB完成版保存フォルダー/Kicadデータ/第一回/Kicker_Bored/kicker_bored.dxf
82.8 x 42.7 mm

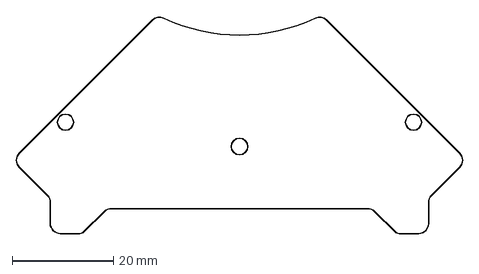
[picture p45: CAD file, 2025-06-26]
JLCPCB完成版保存フォルダー/Kicadデータ/第一回/Power_Bored/Kicker_Bored/kicker_Bored_ver2.dxf
88.1 x 42.9 mm

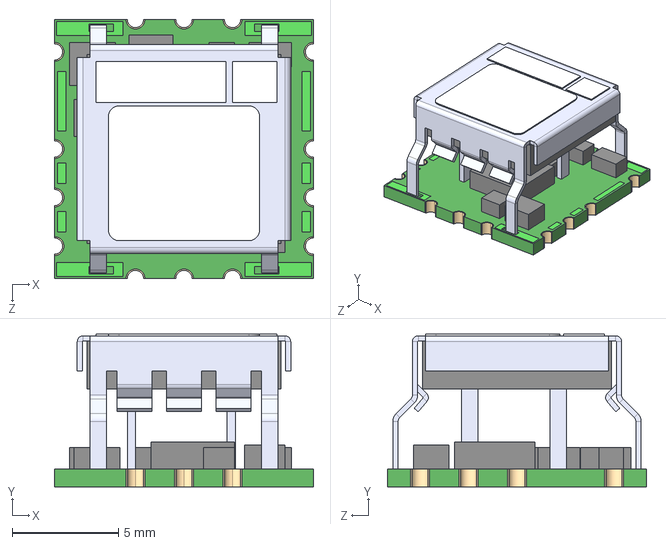
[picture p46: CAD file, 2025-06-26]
JLCPCB完成版保存フォルダー/Kicadデータ/第一回/Power_Bored/OKL-T_6-W12N-C/OKL-T_6-W12N-C.step
12.2 x 7.19 x 12.2 mm

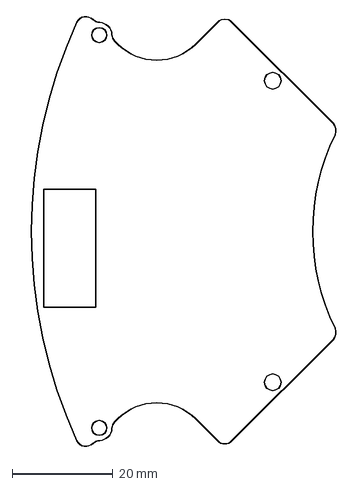
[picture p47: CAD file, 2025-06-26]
JLCPCB完成版保存フォルダー/Kicadデータ/第一回/Power_Bored/power_bored_v1.dxf
63.8 x 85.7 mm

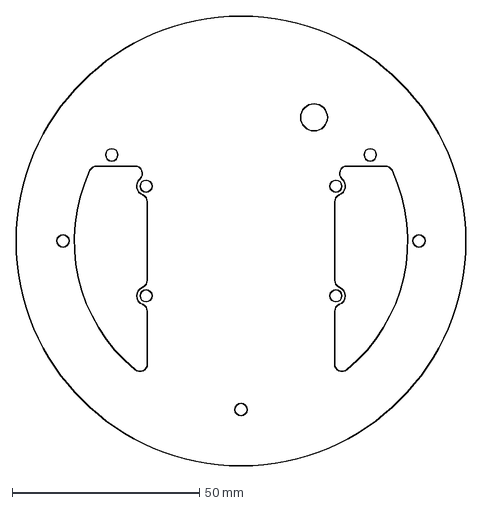
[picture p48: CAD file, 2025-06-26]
JLCPCB完成版保存フォルダー/Kicadデータ/第三回/IR_board/IR_Bored_ver2.dxf
120.0 x 120.0 mm

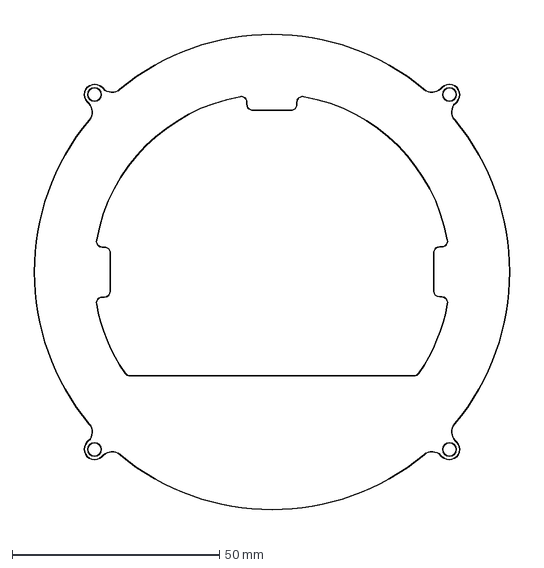
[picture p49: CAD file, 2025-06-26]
JLCPCB完成版保存フォルダー/Kicadデータ/第三回/LINE_Main/スケッチ9.dxf
123.4 x 123.4 mm

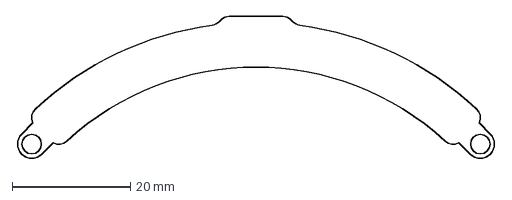
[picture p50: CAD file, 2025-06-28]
JLCPCB完成版保存フォルダー/Kicadデータ/第三回/Line_sensor/LIne_front/Line_front.dxf
81.1 x 24.2 mm

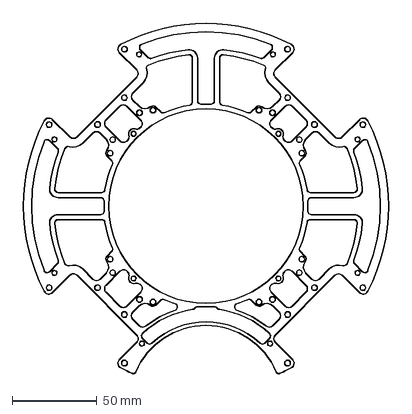
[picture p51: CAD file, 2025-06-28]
JLCPCB完成版保存フォルダー/Kicadデータ/第三回/Line_sensor/Line_line.dxf
224.3 x 211.2 mm

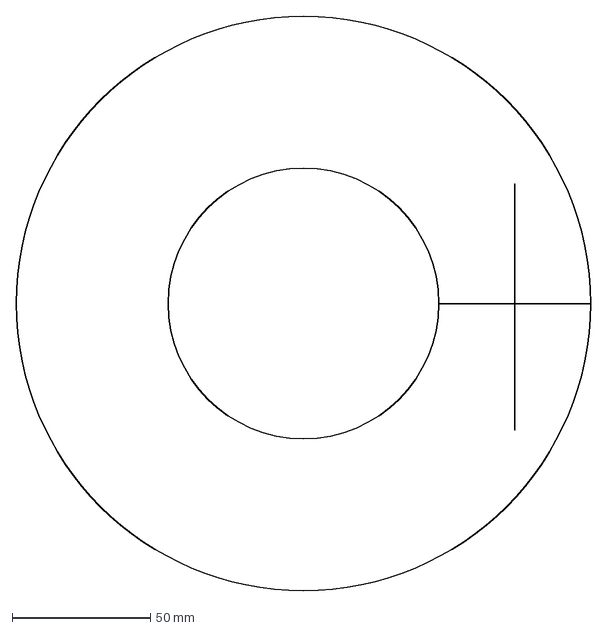
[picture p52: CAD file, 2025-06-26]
JLCPCB完成版保存フォルダー/Kicadデータ/第三回/Main_board/スケッチ6.dxf
208.0 x 208.0 mm

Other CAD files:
JLCPCB完成版保存フォルダー/Kicadデータ/第三回/MainBored/kicker&power.dxf
JLCPCB完成版保存フォルダー/Kicadデータ/第三回/PowerBored/Kicker_Bored/kicker_bored.dxf
JLCPCB完成版保存フォルダー/Kicadデータ/第三回/PowerBored/スケッチ3.dxf
2025/Salvador/TDP/About Hardware/common_data/Frame_underside v16.f3d
2025/Salvador/TDP/About Hardware/common_data/Frame_upperside v15.f3d
2025/Salvador/TDP/About Hardware/common_data/PCB/Line_front v4.f3d
2025/Salvador/TDP/About Hardware/common_data/PCB/Line_sensor_Main v4.f3d
2025/Salvador/TDP/About Hardware/common_data/PCB/Line_side&back v4.f3d
2025/Salvador/TDP/About Hardware/common_data/PCB/Main_board v1.f3d
2025/Salvador/TDP/About Hardware/common_data/PCB/PowerBoard v2.f3z
2025/Salvador/TDP/About Hardware/common_data/battery_case v1.f3z
2025/Salvador/TDP/About Hardware/common_data/dribbler.f3z
2025/Salvador/TDP/About Hardware/common_data/side_cover2 v4.f3z
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

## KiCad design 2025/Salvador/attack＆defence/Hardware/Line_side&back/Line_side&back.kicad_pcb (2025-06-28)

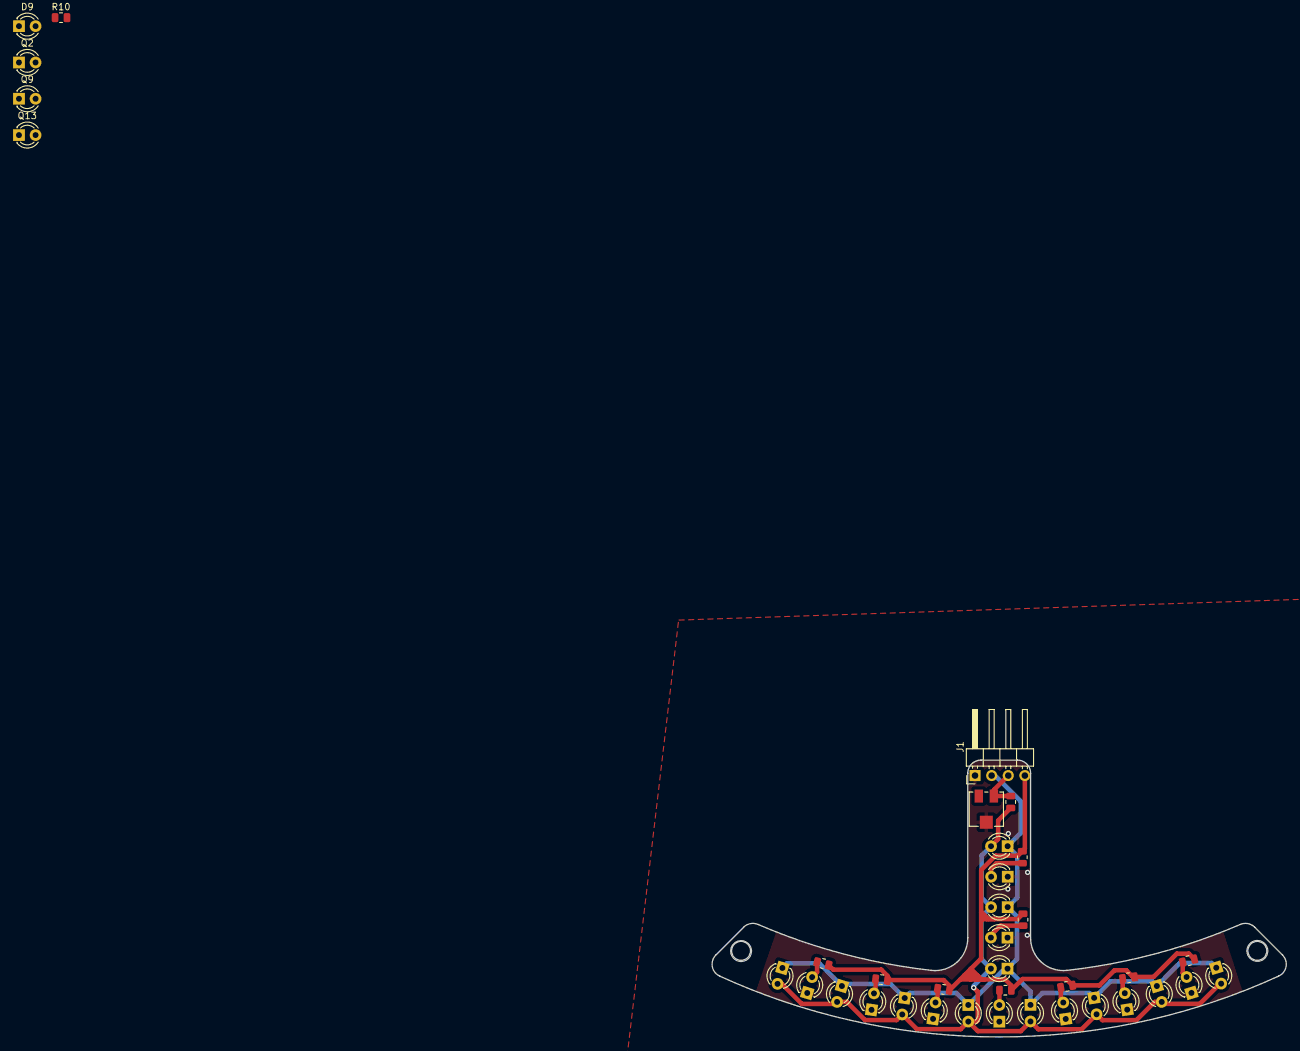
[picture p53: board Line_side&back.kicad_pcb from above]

Board: 2 copper layers, 87.8 x 42.3 mm, 37 parts (0 on the bottom side), 15 nets.

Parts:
D1, D2, D3, D4, D5, D6, D7, D8, D9, D10: LED; LED_D3.0mm_Clear
J1: Conn_01x04_Socket; PinHeader_1x04_P2.54mm_Horizontal
Q1, Q2, Q3, Q4, Q5, Q6, Q7, Q8, Q9, Q10, Q13, Q14, Q15, Q16: Q_Photo_NPN; LED_D3.0mm_Clear
R1, R2, R3, R4, R5, R6, R7, R8, R9, R10, R11: R; R_0805_2012Metric
RV1: R_Potentiometer_Trim_US; Potentiometer_Vishay_TS53YJ_Vertical

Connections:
+3.3V: J1.2, Q1.1 (C), Q2.1 (C), Q3.1 (C), Q4.1 (C), Q5.1 (C), Q6.1 (C), Q7.1 (C), Q8.1 (C), Q9.1 (C), Q10.1 (C), Q13.1 (C), Q14.1 (C), Q15.1 (C), Q16.1 (C)
+5V: J1.4, R1.1, R2.1, R4.1, R5.1, R6.1, R7.1, R8.1, R9.1, R10.1, R11.1
Data_Line_sensor: J1.3, R3.2, RV1.3
GND: D1.1 (K), D2.1 (K), D3.1 (K), D4.1 (K), D5.1 (K), D6.1 (K), D7.1 (K), D8.1 (K), D9.1 (K), D10.1 (K), J1.1, RV1.2
unnamed: D1.2 (A), R1.2
unnamed: D2.2 (A), R2.2
unnamed: D3.2 (A), R4.2
unnamed: D4.2 (A), R5.2
unnamed: D5.2 (A), R6.2
unnamed: D6.2 (A), R7.2
unnamed: D7.2 (A), R8.2
unnamed: D8.2 (A), R9.2
unnamed: D9.2 (A), R10.2
unnamed: D10.2 (A), R11.2
unnamed: Q1.2 (E), Q2.2 (E), Q3.2 (E), Q4.2 (E), Q5.2 (E), Q6.2 (E), Q7.2 (E), Q8.2 (E), Q9.2 (E), Q10.2 (E), Q13.2 (E), Q14.2 (E), Q15.2 (E), Q16.2 (E), R3.1

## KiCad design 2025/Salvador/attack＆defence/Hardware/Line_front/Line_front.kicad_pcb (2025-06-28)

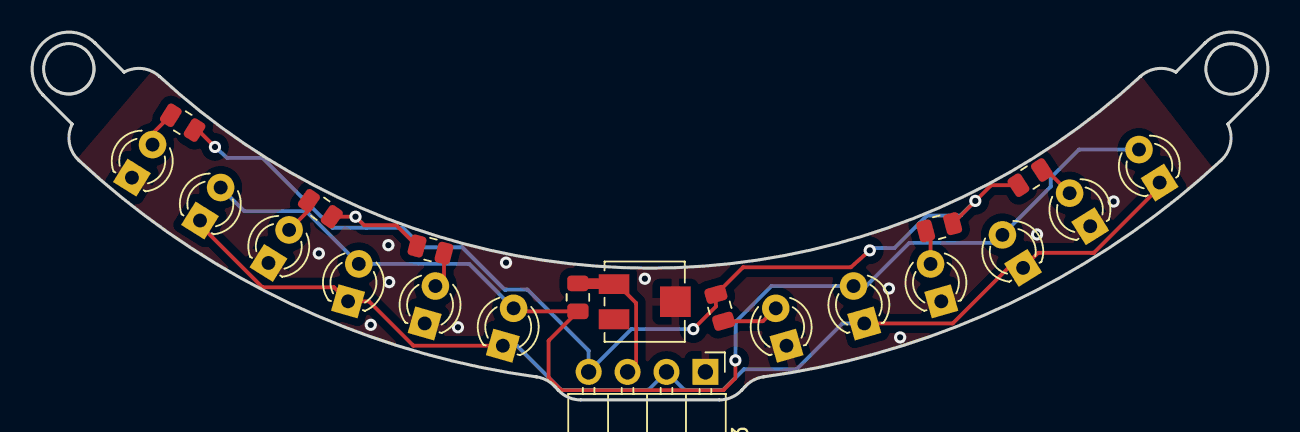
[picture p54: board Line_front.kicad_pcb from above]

Board: 2 copper layers, 80.7 x 24.0 mm, 21 parts (0 on the bottom side), 11 nets.

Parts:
D1, D2, D2#2, D3, D4, D7: LED; LED_D3.0mm_Clear
J3: Conn_01x04_Socket; PinHeader_1x04_P2.54mm_Horizontal
Q1, Q3, Q4, Q15, Q16, Q17: Q_Photo_NPN; LED_D3.0mm_Clear
R1, R1#2, R2, R4, R5, R6, R7: R; R_0805_2012Metric
RV2: R_Potentiometer_Trim_US; Potentiometer_Vishay_TS53YJ_Vertical

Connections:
+3.3V: J3.2, Q1.1 (C), Q3.1 (C), Q4.1 (C), Q15.1 (C), Q16.1 (C), Q17.1 (C)
+5V: J3.4, R1.1, R1#2.1, R2.1, R5.1, R6.1, R7.1
Data_Line_sensor: J3.3, R4.2, RV2.3
GND: D1.1 (K), D2.1 (K), D2#2.1 (K), D3.1 (K), D4.1 (K), D7.1 (K), J3.1, RV2.2
unnamed: D1.2 (A), R1#2.2
unnamed: D2#2.2 (A), R5.2
unnamed: D3.2 (A), R6.2
unnamed: D4.2 (A), R7.2
unnamed: D7.2 (A), R2.2
unnamed: D2.2 (A), R1.2
unnamed: Q1.2 (E), Q3.2 (E), Q4.2 (E), Q15.2 (E), Q16.2 (E), Q17.2 (E), R4.1

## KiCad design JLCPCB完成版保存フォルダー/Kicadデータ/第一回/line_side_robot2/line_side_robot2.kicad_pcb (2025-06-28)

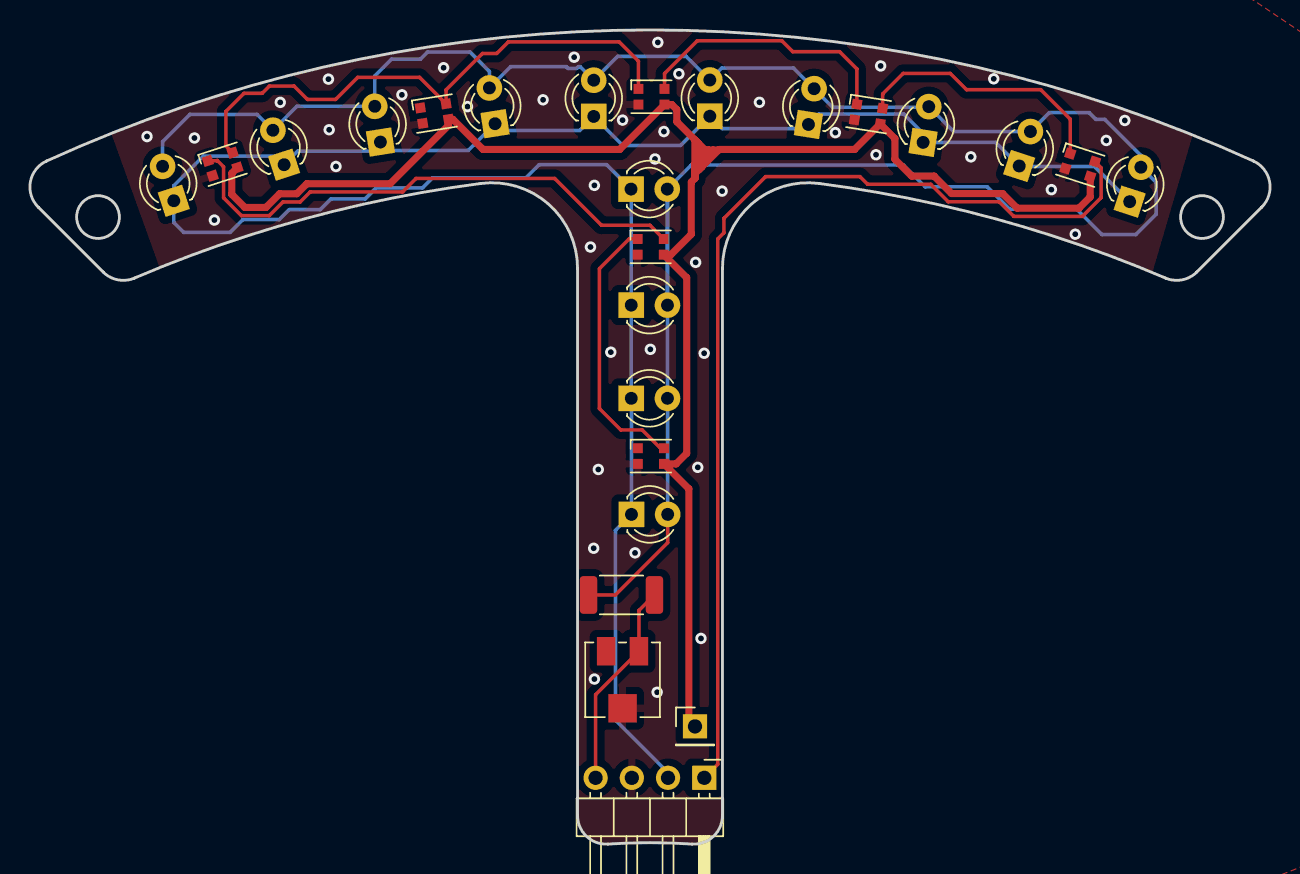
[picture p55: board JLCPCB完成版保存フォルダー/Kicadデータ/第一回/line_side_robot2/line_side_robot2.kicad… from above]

Board: 2 copper layers, 87.0 x 57.1 mm, 25 parts (0 on the bottom side), 11 nets.

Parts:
D1, D2, D3, D4, D4#2, D5, D6: NeoPixel_THT; LED_WS2812B-2020_PLCC4_2.0x2.0mm
J1: Conn_01x04_Pin; PinHeader_1x04_P2.54mm_Horizontal
J2: Conn_01x01_Pin; PinHeader_1x01_P2.54mm_Vertical
Q1, Q2, Q3, Q4, Q5, Q6, Q7, Q8, Q9, Q10, Q11, Q12, Q13, Q14: Q_Photo_NPN; LED_D3.0mm_Clear
R1: 1K; R_2010_5025Metric
RV1: R_Potentiometer_Trim_US; Potentiometer_Vishay_TS53YJ_Vertical

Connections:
+3.3V: J1.2, Q1.1 (C), Q2.1 (C), Q3.1 (C), Q4.1 (C), Q5.1 (C), Q6.1 (C), Q7.1 (C), Q8.1 (C), Q9.1 (C), Q10.1 (C), Q11.1 (C), Q12.1 (C), Q13.1 (C), Q14.1 (C)
+5V: D1.3 (VDD), D2.3 (VDD), D3.3 (VDD), D4.3 (VDD), D4#2.3 (VDD), D5.3 (VDD), D6.3 (VDD), J2.1
/PWM: D1.4 (DIN), J1.1
/S: J1.4, R1.1, RV1.3
GND: D1.2 (GND), D2.2 (GND), D3.2 (GND), D4.2 (GND), D4#2.2 (GND), D5.2 (GND), D6.2 (GND), J1.3, RV1.2
unnamed: D1.1 (DOUT), D2.4 (DIN)
unnamed: D2.1 (DOUT), D3.4 (DIN)
unnamed: D3.1 (DOUT), D4.4 (DIN), D6.4 (DIN)
unnamed: D4#2.4 (DIN), D6.1 (DOUT)
unnamed: D4#2.1 (DOUT), D5.4 (DIN)
unnamed: Q1.2 (E), Q2.2 (E), Q3.2 (E), Q4.2 (E), Q5.2 (E), Q6.2 (E), Q7.2 (E), Q8.2 (E), Q9.2 (E), Q10.2 (E), Q11.2 (E), Q12.2 (E), Q13.2 (E), Q14.2 (E), R1.2

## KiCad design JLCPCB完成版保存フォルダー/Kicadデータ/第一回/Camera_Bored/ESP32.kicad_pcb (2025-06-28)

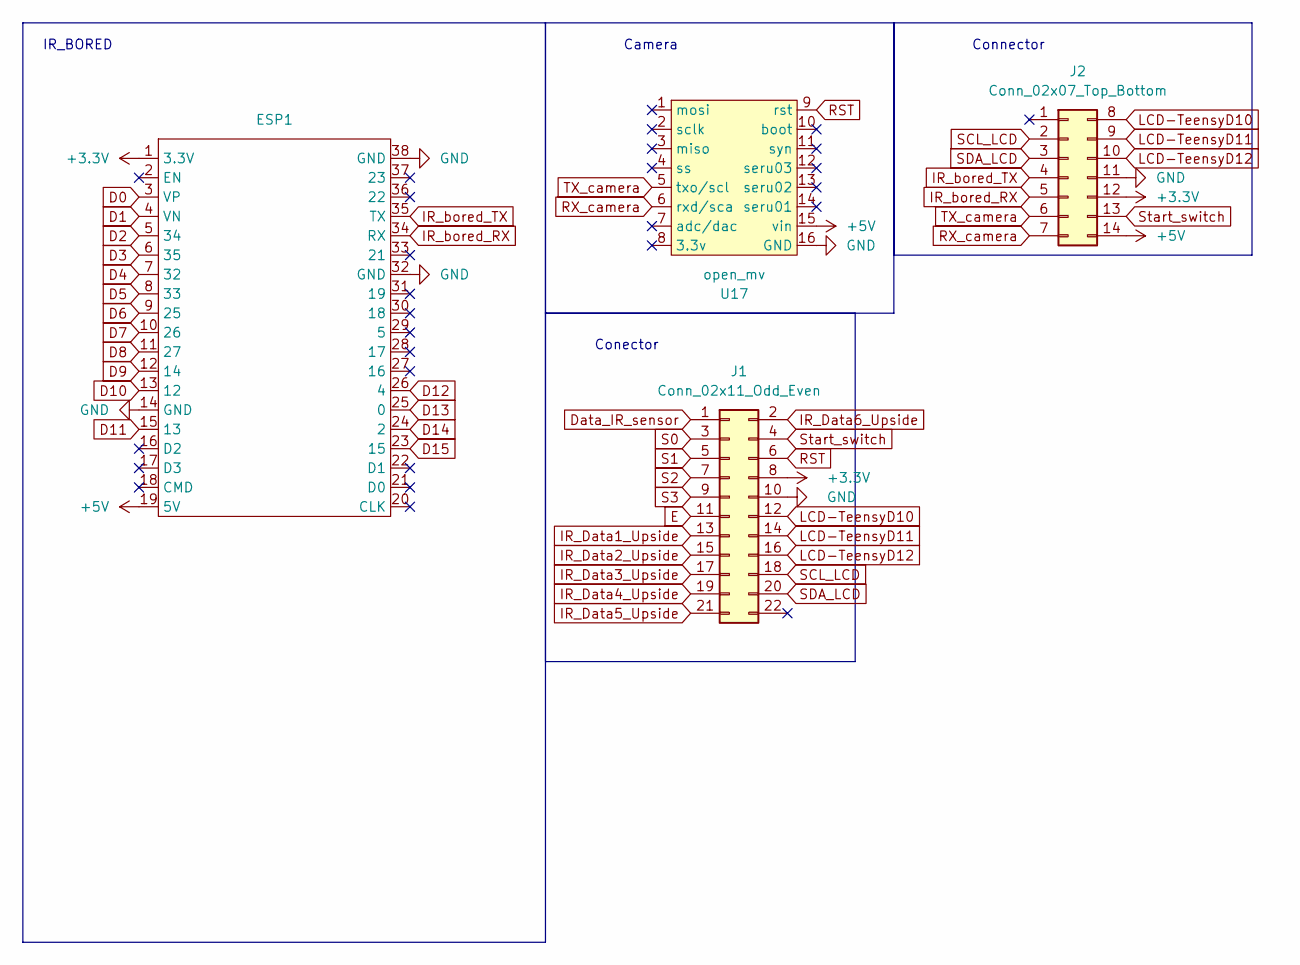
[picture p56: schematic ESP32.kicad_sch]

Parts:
ESP1: ESP32-DevKitC
J1: Conn_02x11_Odd_Even; PinHeader_2x11_P2.54mm_Vertical
J2: Conn_02x07_Top_Bottom; IDC-Header_2x07_P2.54mm_Vertical
U17: open_mv; OpenMV

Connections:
+3.3V: ESP1.1 (3.3V), J1.8, J2.12
+5V: ESP1.19 (5V), J2.14, U17.15 (vin)
D0: ESP1.3 (VP)
D1: ESP1.4 (VN)
D2: ESP1.5 (34)
D3: ESP1.6 (35)
D4: ESP1.7 (32)
D5: ESP1.8 (33)
D6: ESP1.9 (25)
D7: ESP1.10 (26)
D8: ESP1.11 (27)
D9: ESP1.12 (14)
D10: ESP1.13 (12)
D11: ESP1.15 (13)
D12: ESP1.26 (4)
D13: ESP1.25 (0)
D14: ESP1.24 (2)
D15: ESP1.23 (15)
Data_IR_sensor: J1.1
E: J1.11
GND: ESP1.14 (GND), ESP1.32 (GND), ESP1.38 (GND), J1.10, J2.11, U17.16 (GND)
IR_Data1_Upside: J1.13
IR_Data2_Upside: J1.15
IR_Data3_Upside: J1.17
IR_Data4_Upside: J1.19
IR_Data5_Upside: J1.21
IR_Data6_Upside: J1.2
IR_bored_RX: ESP1.34 (RX), J2.5
IR_bored_TX: ESP1.35 (TX), J2.4
LCD-TeensyD10: J1.12, J2.8
LCD-TeensyD11: J1.14, J2.9
LCD-TeensyD12: J1.16, J2.10
RST: J1.6, U17.9 (rst)
RX_camera: J2.7, U17.6 (rxd/sca)
S0: J1.3
S1: J1.5
S2: J1.7
S3: J1.9
SCL_LCD: J1.18, J2.2
SDA_LCD: J1.20, J2.3
Start_switch: J1.4, J2.13
TX_camera: J2.6, U17.5 (txo/scl)

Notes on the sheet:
Connector
Conector
IR_BORED
Camera

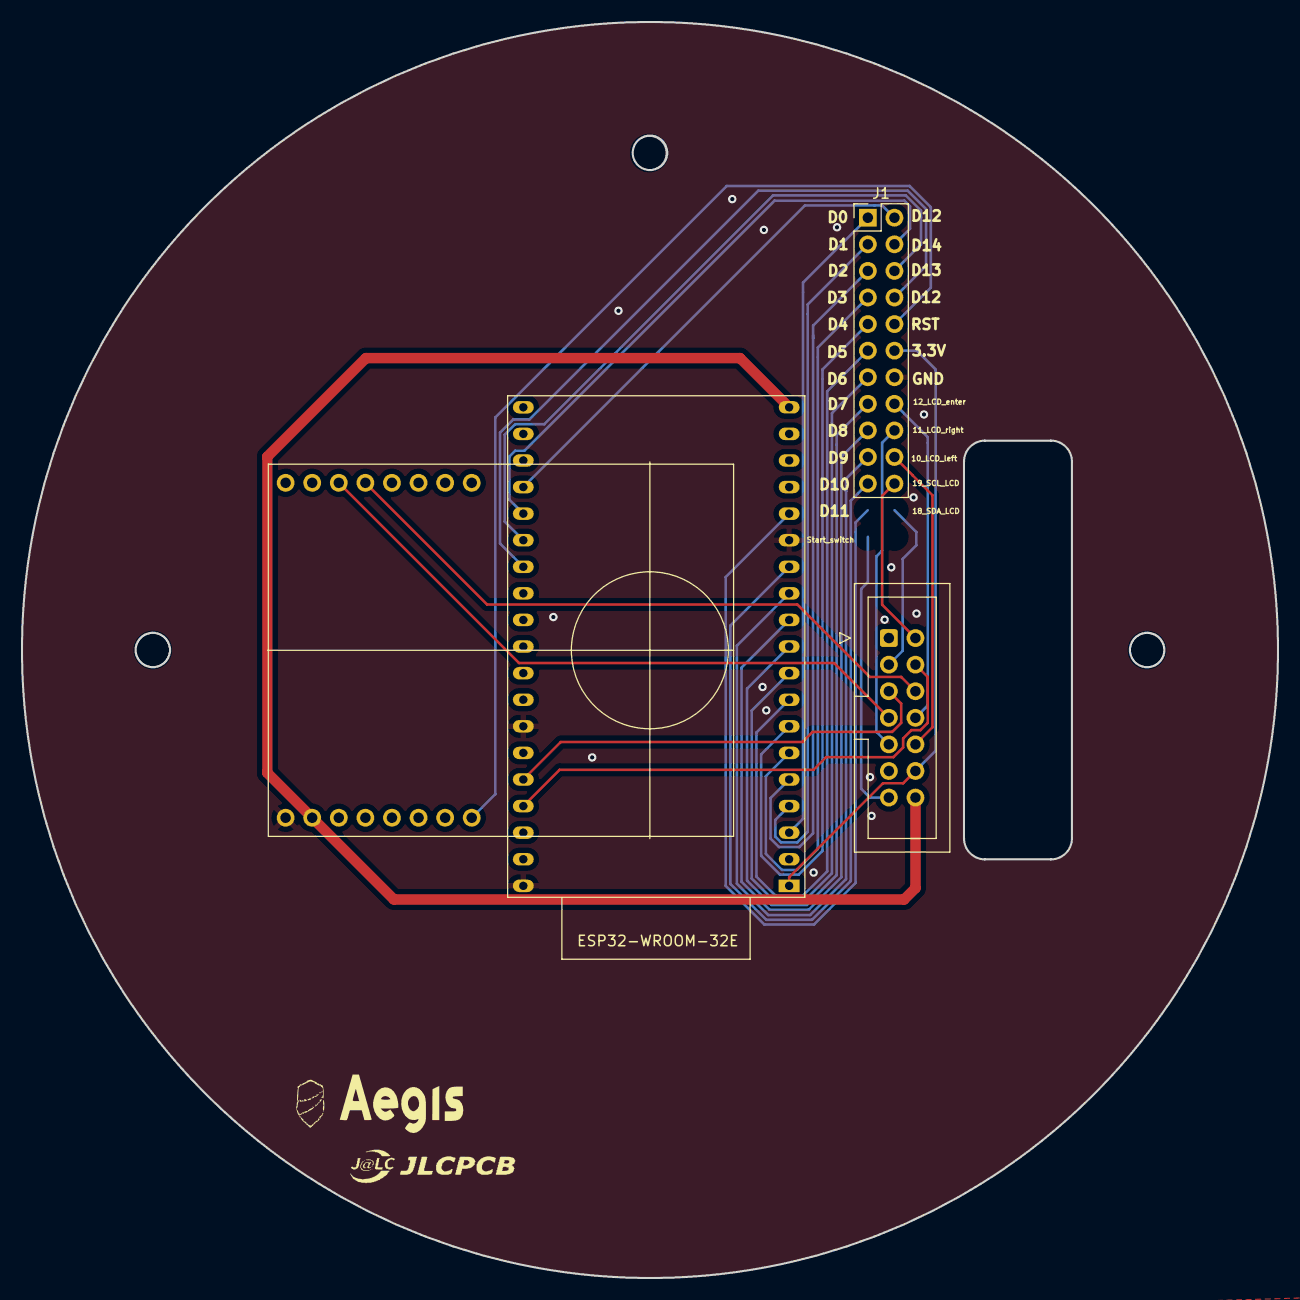
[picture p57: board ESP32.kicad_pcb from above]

Board: 2 copper layers, 120.0 x 120.0 mm, 4 parts (0 on the bottom side), 14 nets.

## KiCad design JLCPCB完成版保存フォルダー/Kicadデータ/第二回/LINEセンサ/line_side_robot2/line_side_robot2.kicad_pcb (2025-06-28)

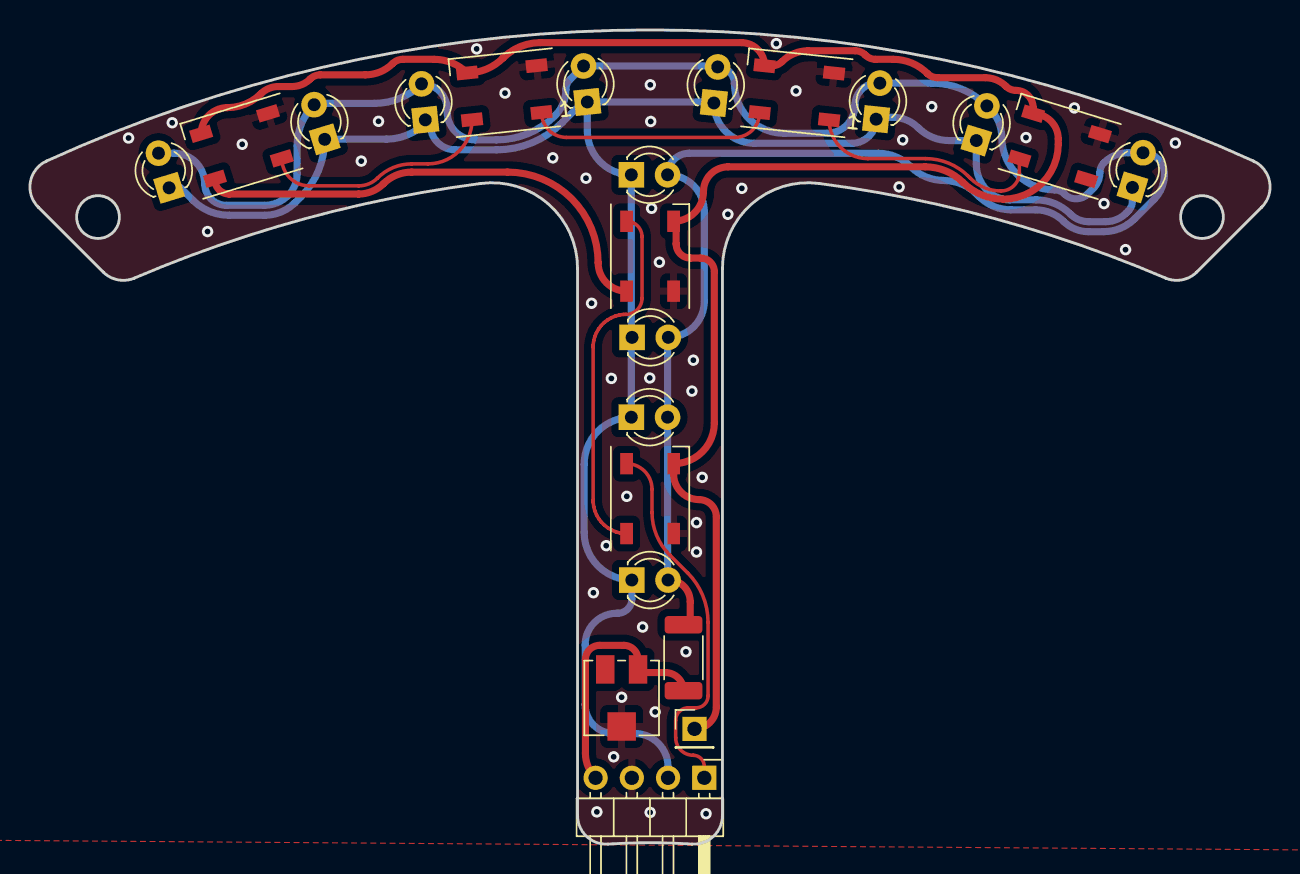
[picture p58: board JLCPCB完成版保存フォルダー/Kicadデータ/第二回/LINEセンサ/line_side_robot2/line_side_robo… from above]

Board: 2 copper layers, 87.0 x 57.1 mm, 22 parts (0 on the bottom side), 11 nets.

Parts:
D1, D2, D3, D4, D5, D6: NeoPixel_THT; LED_WS2812B_PLCC4_5.0x5.0mm_P3.2mm
J1: Conn_01x04_Pin; PinHeader_1x04_P2.54mm_Horizontal
J2: Conn_01x01_Pin; PinHeader_1x01_P2.54mm_Vertical
Q1, Q2, Q3, Q4, Q5, Q6, Q7, Q8, Q9, Q10, Q11, Q12: Q_Photo_NPN; LED_D3.0mm_Clear
R1: 1K; R_2010_5025Metric
RV1: R_Potentiometer_Trim_US; Potentiometer_Vishay_TS53YJ_Vertical

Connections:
+3.3V: J1.2, Q1.1 (C), Q2.1 (C), Q3.1 (C), Q4.1 (C), Q5.1 (C), Q6.1 (C), Q7.1 (C), Q8.1 (C), Q9.1 (C), Q10.1 (C), Q11.1 (C), Q12.1 (C)
+5V: D1.3 (VDD), D2.3 (VDD), D3.3 (VDD), D4.3 (VDD), D5.3 (VDD), D6.3 (VDD), J2.1
/PWM: D1.4 (DIN), J1.1
/S: J1.4, R1.1, RV1.3
GND: D1.2 (GND), D2.2 (GND), D3.2 (GND), D4.2 (GND), D5.2 (GND), D6.2 (GND), J1.3, RV1.2
unnamed: D1.1 (DOUT), D2.4 (DIN)
unnamed: D2.1 (DOUT), D3.4 (DIN)
unnamed: D3.1 (DOUT), D6.4 (DIN)
unnamed: D4.4 (DIN), D6.1 (DOUT)
unnamed: D4.1 (DOUT), D5.4 (DIN)
unnamed: Q1.2 (E), Q2.2 (E), Q3.2 (E), Q4.2 (E), Q5.2 (E), Q6.2 (E), Q7.2 (E), Q8.2 (E), Q9.2 (E), Q10.2 (E), Q11.2 (E), Q12.2 (E), R1.2

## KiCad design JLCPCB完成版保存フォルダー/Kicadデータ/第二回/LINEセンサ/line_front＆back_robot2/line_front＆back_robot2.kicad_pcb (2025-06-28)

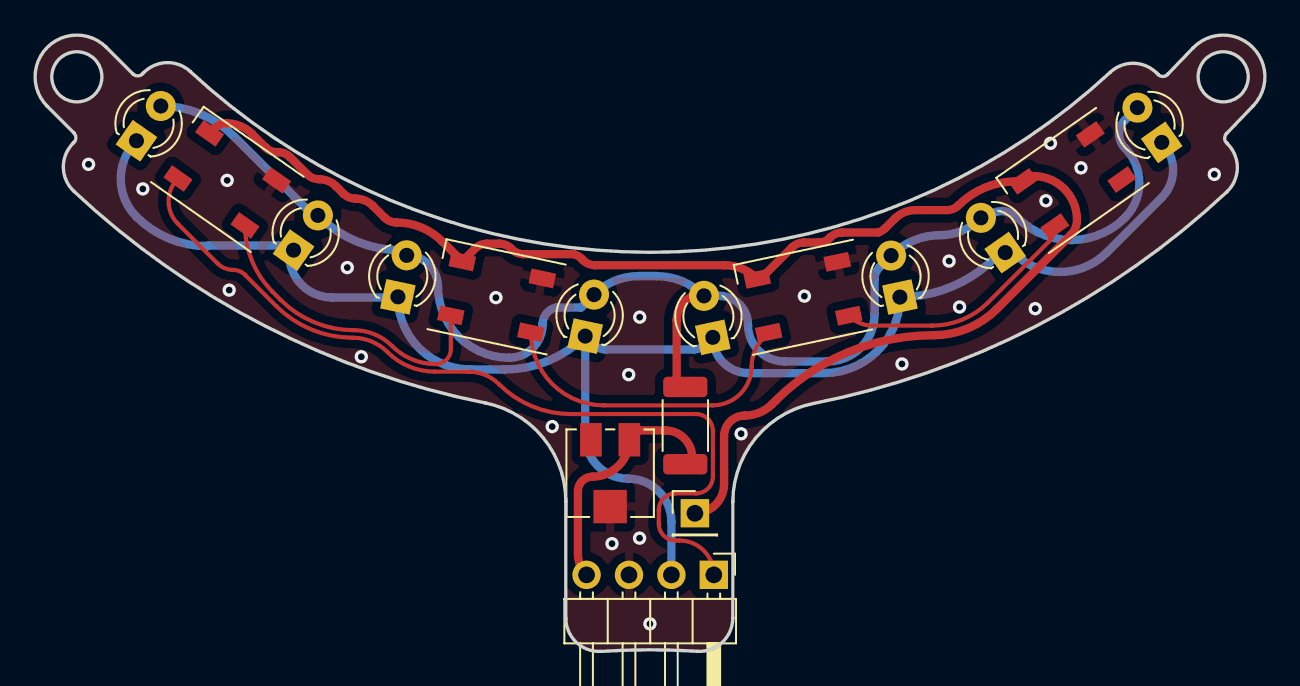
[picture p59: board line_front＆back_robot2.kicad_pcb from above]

Board: 2 copper layers, 73.6 x 36.9 mm, 16 parts (0 on the bottom side), 9 nets.

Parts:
D1, D2, D3, D5: NeoPixel_THT; LED_WS2812B_PLCC4_5.0x5.0mm_P3.2mm
J2: Conn_01x04_Pin; PinHeader_1x04_P2.54mm_Horizontal
J3: Conn_01x01_Pin; PinHeader_1x01_P2.54mm_Vertical
Q1, Q2, Q3, Q4, Q7, Q8, Q9, Q10: Q_Photo_NPN; LED_D3.0mm_Clear
R8: 1K; R_2010_5025Metric
RV2: R_Potentiometer_Trim_US; Potentiometer_Vishay_TS53YJ_Vertical

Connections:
+3.3V: J2.2, Q1.1 (C), Q2.1 (C), Q3.1 (C), Q4.1 (C), Q7.1 (C), Q8.1 (C), Q9.1 (C), Q10.1 (C)
+5V: D1.3 (VDD), D2.3 (VDD), D3.3 (VDD), D5.3 (VDD), J3.1
/PWM: D3.4 (DIN), J2.1
/S: J2.4, R8.1, RV2.3
GND: D1.2 (GND), D2.2 (GND), D3.2 (GND), D5.2 (GND), J2.3, RV2.2
unnamed: D1.4 (DIN), D5.1 (DOUT)
unnamed: D2.4 (DIN), D3.1 (DOUT)
unnamed: D2.1 (DOUT), D5.4 (DIN)
unnamed: Q1.2 (E), Q2.2 (E), Q3.2 (E), Q4.2 (E), Q7.2 (E), Q8.2 (E), Q9.2 (E), Q10.2 (E), R8.2

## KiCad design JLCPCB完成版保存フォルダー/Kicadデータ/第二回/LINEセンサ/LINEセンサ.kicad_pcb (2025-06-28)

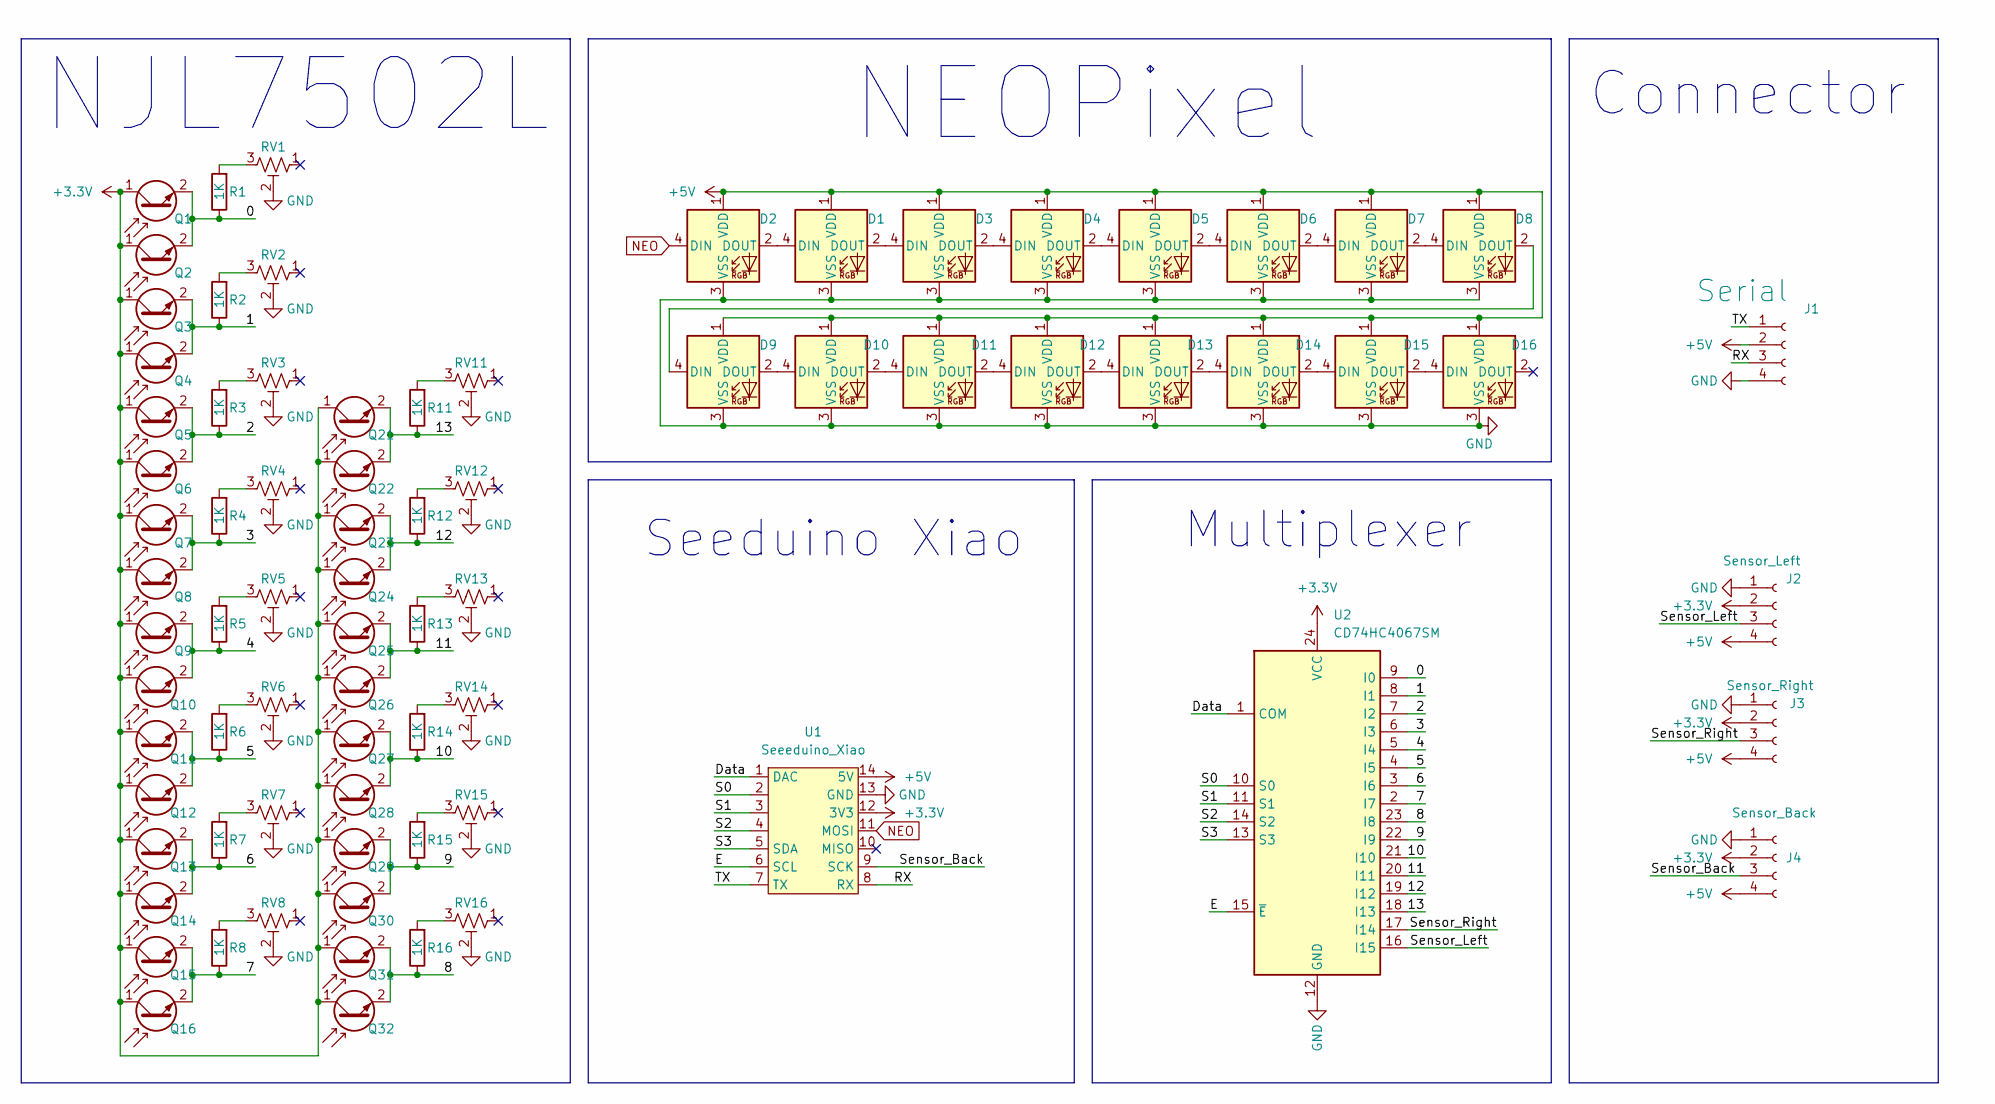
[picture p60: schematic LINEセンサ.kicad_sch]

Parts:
D1: WS2812B; JST_XH_B4B-XH-A_1x04_P2.50mm_Vertical
D2, D3, D4, D5, D6, D7, D8, D9, D10, D11, D12, D13, D14, D15, D16: WS2812B; LED_WS2812B-2020_PLCC4_2.0x2.0mm
J1: Serial; JST_XH_B4B-XH-A_1x04_P2.50mm_Vertical
J2: Sensor_Left; JST_XH_B4B-XH-A_1x04_P2.50mm_Vertical
J3: Sensor_Right; JST_XH_B4B-XH-A_1x04_P2.50mm_Vertical
J4: Sensor_Back; JST_XH_B4B-XH-A_1x04_P2.50mm_Vertical
Q1, Q2, Q3, Q4, Q5, Q6, Q7, Q8, Q9, Q10, Q11, Q12, Q13, Q14, Q15, Q16, Q21, Q22, Q23, Q24, Q25, Q26, Q27, Q28, Q29, Q30, Q31, Q32: Q_Photo_NPN; LED_D3.0mm_Clear
R1, R2, R3, R4, R5, R6, R7, R8, R11, R12, R13, R14, R15, R16: 1K; R_2010_5025Metric
RV1, RV2, RV3, RV4, RV5, RV6, RV7, RV8, RV11, RV12, RV13, RV14, RV15, RV16: R_Potentiometer_Trim_US; Potentiometer_Vishay_TS53YJ_Vertical
U1: Seeeduino_Xiao; seeeduinoXIAO
U2: CD74HC4067SM; SSOP-24_5.3x8.2mm_P0.65mm

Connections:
+3.3V: J2.2, J3.2, J4.2, Q1.1 (C), Q2.1 (C), Q3.1 (C), Q4.1 (C), Q5.1 (C), Q6.1 (C), Q7.1 (C), Q8.1 (C), Q9.1 (C), Q10.1 (C), Q11.1 (C), Q12.1 (C), Q13.1 (C), Q14.1 (C), Q15.1 (C), Q16.1 (C), Q21.1 (C), Q22.1 (C), Q23.1 (C), Q24.1 (C), Q25.1 (C), Q26.1 (C), Q27.1 (C), Q28.1 (C), Q29.1 (C), Q30.1 (C), Q31.1 (C), Q32.1 (C), U1.12 (3V3), U2.24 (VCC)
+5V: D1.1 (VDD), D2.1 (VDD), D3.1 (VDD), D4.1 (VDD), D5.1 (VDD), D6.1 (VDD), D7.1 (VDD), D8.1 (VDD), D9.1 (VDD), D10.1 (VDD), D11.1 (VDD), D12.1 (VDD), D13.1 (VDD), D14.1 (VDD), D15.1 (VDD), D16.1 (VDD), J1.2, J2.4, J3.4, J4.4, U1.14 (5V)
/0: Q1.2 (E), Q2.2 (E), R1.1, U2.9 (I0)
/1: Q3.2 (E), Q4.2 (E), R2.1, U2.8 (I1)
/2: Q5.2 (E), Q6.2 (E), R3.1, U2.7 (I2)
/3: Q7.2 (E), Q8.2 (E), R4.1, U2.6 (I3)
/4: Q9.2 (E), Q10.2 (E), R5.1, U2.5 (I4)
/5: Q11.2 (E), Q12.2 (E), R6.1, U2.4 (I5)
/6: Q13.2 (E), Q14.2 (E), R7.1, U2.3 (I6)
/7: Q15.2 (E), Q16.2 (E), R8.1, U2.2 (I7)
/8: Q31.2 (E), Q32.2 (E), R16.1, U2.23 (I8)
/9: Q29.2 (E), Q30.2 (E), R15.1, U2.22 (I9)
/10: Q27.2 (E), Q28.2 (E), R14.1, U2.21 (I10)
/11: Q25.2 (E), Q26.2 (E), R13.1, U2.20 (I11)
/12: Q23.2 (E), Q24.2 (E), R12.1, U2.19 (I12)
/13: Q21.2 (E), Q22.2 (E), R11.1, U2.18 (I13)
/Data: U1.1 (DAC), U2.1 (COM)
/E: U1.6 (SCL), U2.15 (~E)
/RX: J1.3, U1.8 (RX)
/S0: U1.2, U2.10 (S0)
/S1: U1.3, U2.11 (S1)
/S2: U1.4, U2.14 (S2)
/S3: U1.5 (SDA), U2.13 (S3)
/Sensor_Back: J4.3, U1.9 (SCK)
/Sensor_Left: J2.3, U2.16 (I15)
/Sensor_Right: J3.3, U2.17 (I14)
/TX: J1.1, U1.7 (TX)
GND: D1.3 (VSS), D2.3 (VSS), D3.3 (VSS), D4.3 (VSS), D5.3 (VSS), D6.3 (VSS), D7.3 (VSS), D8.3 (VSS), D9.3 (VSS), D10.3 (VSS), D11.3 (VSS), D12.3 (VSS), D13.3 (VSS), D14.3 (VSS), D15.3 (VSS), D16.3 (VSS), J1.4, J2.1, J3.1, J4.1, RV1.2, RV2.2, RV3.2, RV4.2, RV5.2, RV6.2, RV7.2, RV8.2, RV11.2, RV12.2, RV13.2, RV14.2, RV15.2, RV16.2, U1.13 (GND), U2.12 (GND)
NEO: D2.4 (DIN), U1.11 (MOSI)
unnamed: D1.4 (DIN), D2.2 (DOUT)
unnamed: D1.2 (DOUT), D3.4 (DIN)
unnamed: D3.2 (DOUT), D4.4 (DIN)
unnamed: D4.2 (DOUT), D5.4 (DIN)
unnamed: D5.2 (DOUT), D6.4 (DIN)
unnamed: D6.2 (DOUT), D7.4 (DIN)
unnamed: D7.2 (DOUT), D8.4 (DIN)
unnamed: D8.2 (DOUT), D9.4 (DIN)
unnamed: D9.2 (DOUT), D10.4 (DIN)
unnamed: D10.2 (DOUT), D11.4 (DIN)
unnamed: D11.2 (DOUT), D12.4 (DIN)
unnamed: D12.2 (DOUT), D13.4 (DIN)
unnamed: D13.2 (DOUT), D14.4 (DIN)
unnamed: D14.2 (DOUT), D15.4 (DIN)
unnamed: D15.2 (DOUT), D16.4 (DIN)
unnamed: R1.2, RV1.3
unnamed: R2.2, RV2.3
unnamed: R3.2, RV3.3
unnamed: R4.2, RV4.3
unnamed: R5.2, RV5.3
unnamed: R6.2, RV6.3
unnamed: R7.2, RV7.3
unnamed: R8.2, RV8.3
unnamed: R11.2, RV11.3
unnamed: R12.2, RV12.3
unnamed: R13.2, RV13.3
unnamed: R14.2, RV14.3
unnamed: R15.2, RV15.3
unnamed: R16.2, RV16.3

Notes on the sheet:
NJL7502L
Seeduino Xiao
NEOPixel
Multiplexer
Connector

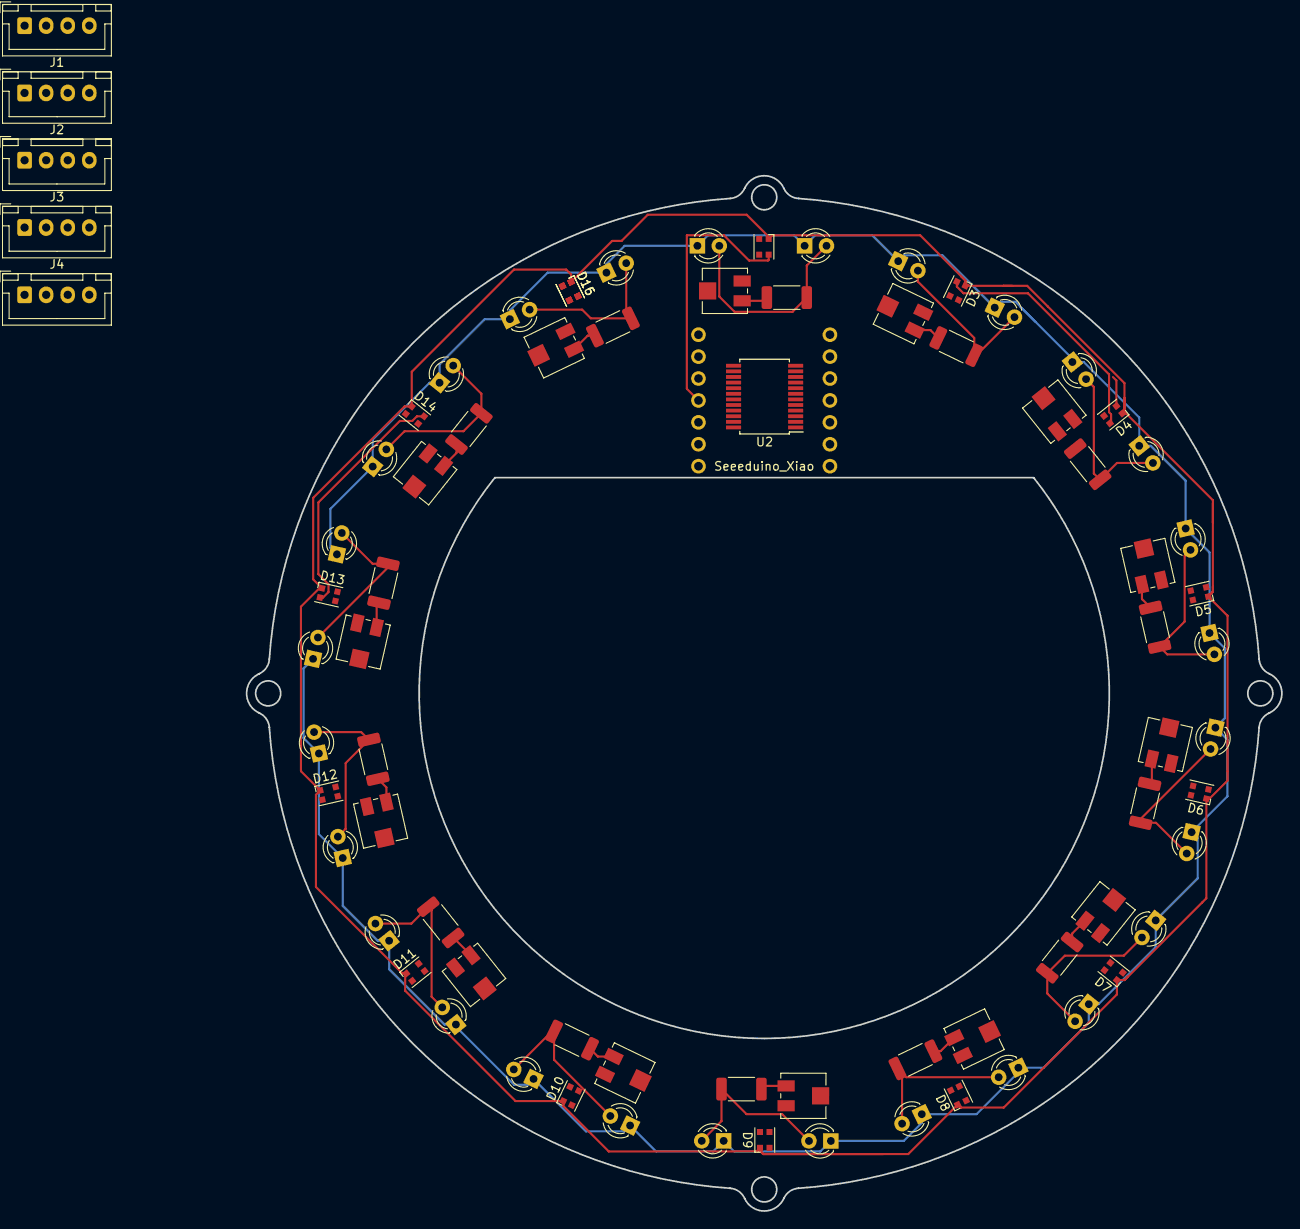
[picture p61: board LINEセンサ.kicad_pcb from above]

Board: 2 copper layers, 120.0 x 120.0 mm, 78 parts (0 on the bottom side), 58 nets.

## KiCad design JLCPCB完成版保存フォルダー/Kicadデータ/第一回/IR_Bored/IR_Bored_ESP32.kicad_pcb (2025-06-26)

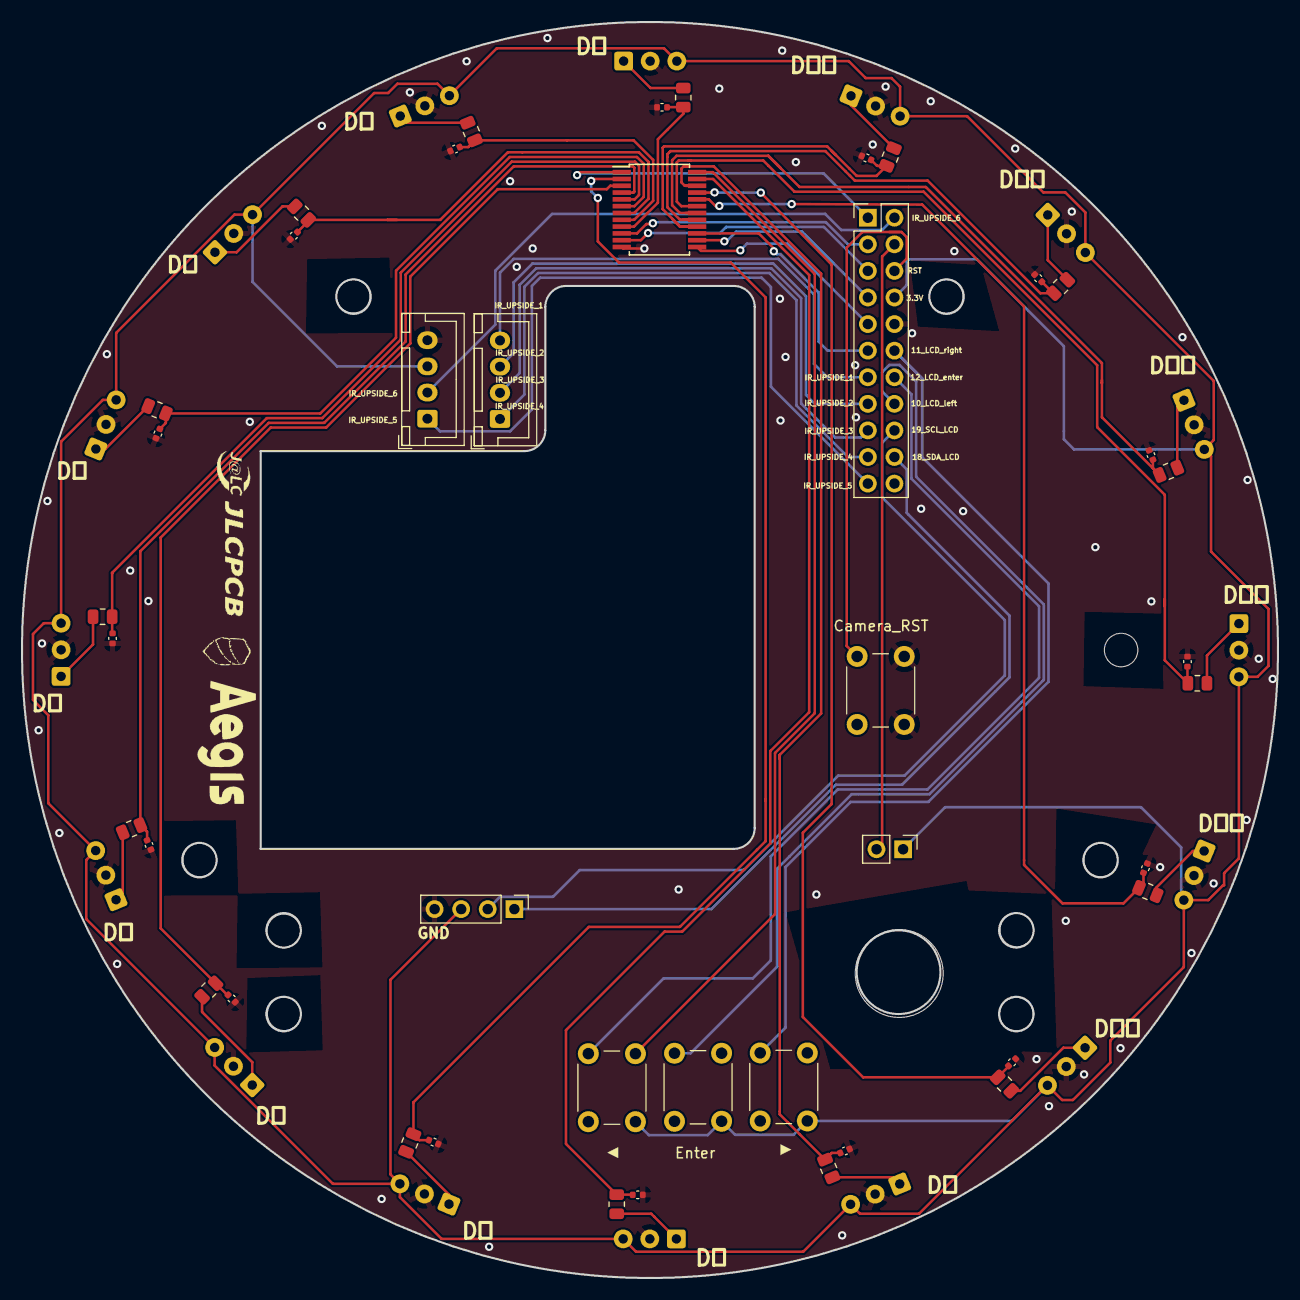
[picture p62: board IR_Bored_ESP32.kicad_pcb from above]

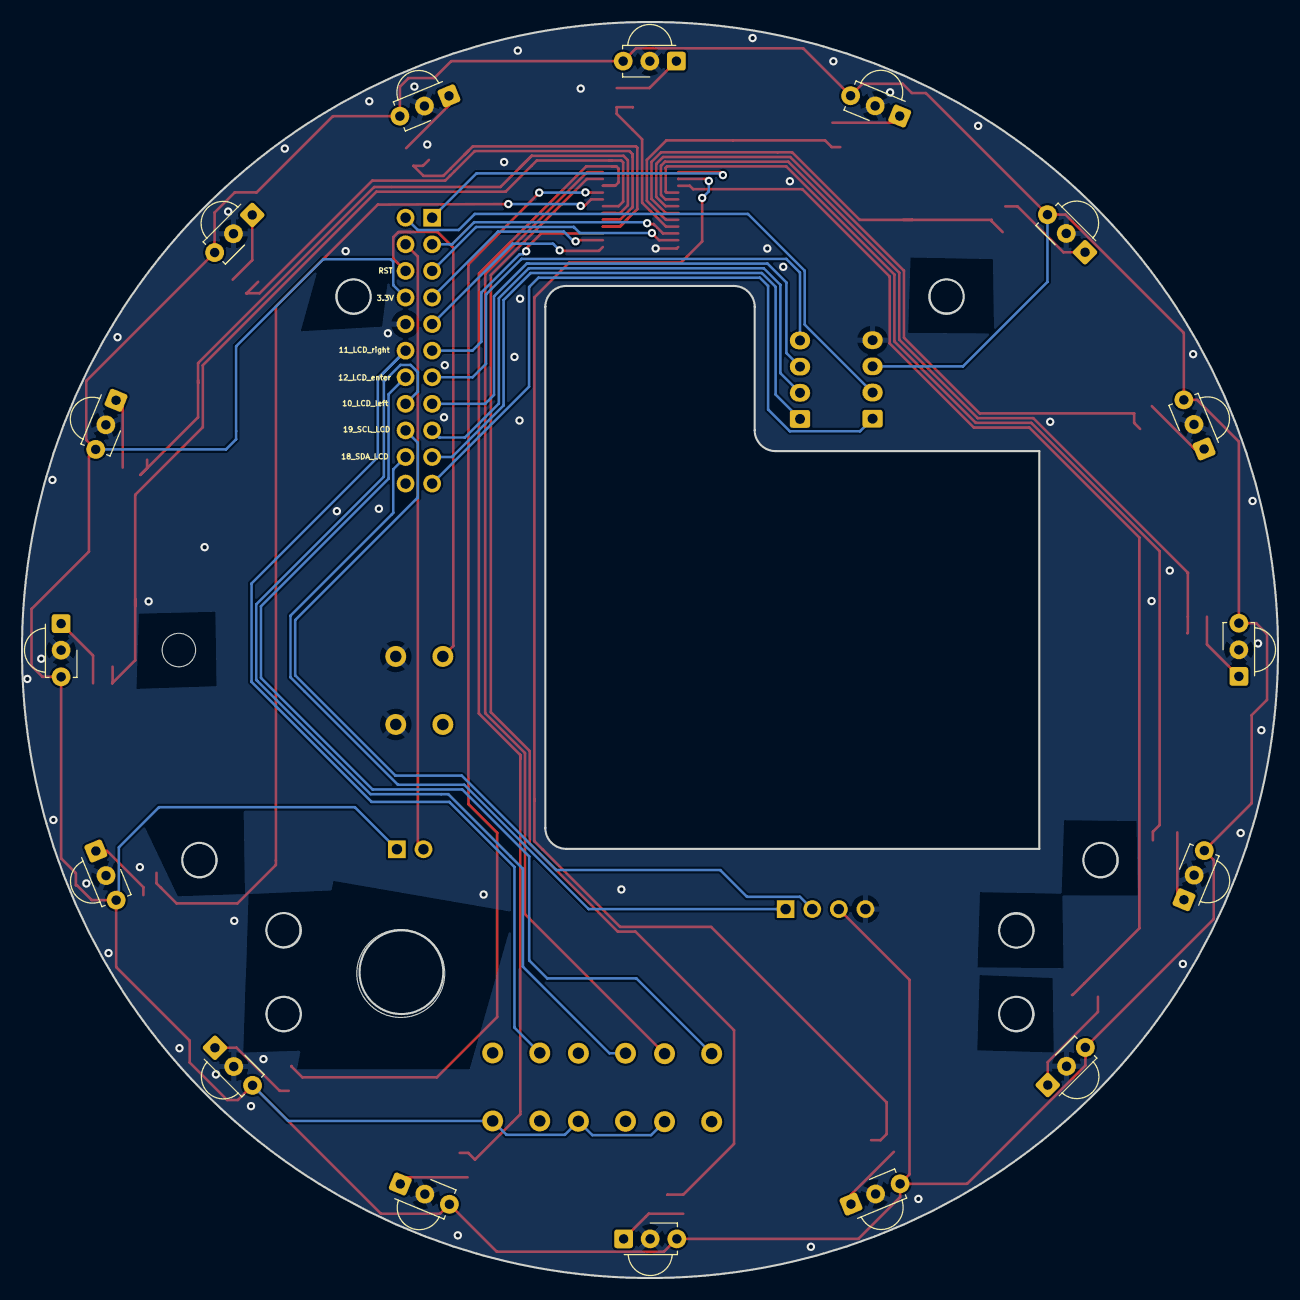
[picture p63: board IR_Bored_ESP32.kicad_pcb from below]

Board: 2 copper layers, 120.0 x 120.0 mm, 58 parts (16 on the bottom side), 53 nets.

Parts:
C1, C2, C3, C4, C5, C6, C7, C8, C9, C10, C11, C12, C13, C14, C15, C16: 104; C_0402_1005Metric
Camera_RST: SW_DIP_x01; SW_PUSH_6mm_H5mm
J1: Conn_01x04_Socket; PinHeader_1x04_P2.54mm_Vertical
J2, J3: Conn_01x04_Pin; JST_XH_B4B-XH-A_1x04_P2.50mm_Vertical
J4: Conn_02x11_Odd_Even; PinHeader_2x11_P2.54mm_Vertical
R1, R2, R3, R4, R5, R6, R7, R8, R9, R10, R11, R12, R13, R14, R15, R16: 22k; R_0805_2012Metric
SW1, SW2, SW3: LCD; SW_PUSH_6mm_H5mm
SW5: SW_DIP_x01; PinHeader_1x02_P2.54mm_Vertical
U1, U2, U3, U4, U5, U6, U7, U8, U9, U10, U11, U12, U13, U14, U15, U17: TSSP58P38; Vishay_MINICAST-3Pin
U16: CD74HC4067SM; SSOP-24_5.3x8.2mm_P0.65mm

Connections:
+3.3V: J1.3, J3.3, J4.8, SW1.2, SW2.2, SW3.2, SW5.1, U1.3 (Vs), U2.3 (Vs), U3.3 (Vs), U4.3 (Vs), U5.3 (Vs), U6.3 (Vs), U7.3 (Vs), U8.3 (Vs), U9.3 (Vs), U10.3 (Vs), U11.3 (Vs), U12.3 (Vs), U13.3 (Vs), U14.3 (Vs), U15.3 (Vs), U16.24 (VCC), U17.3 (Vs)
D0: C3.1, R3.1, U16.9 (I0)
D1: C4.1, R4.1, U16.8 (I1)
D2: C1.1, R1.1, U16.7 (I2)
D3: C2.1, R2.1, U16.6 (I3)
D4: C5.1, R5.1, U16.5 (I4)
D5: C6.1, R6.1, U16.4 (I5)
D6: C7.1, R7.1, U16.3 (I6)
D7: C8.1, R8.1, U16.2 (I7)
D8: C11.1, R11.1, U16.23 (I8)
D9: C12.1, R12.1, U16.22 (I9)
D10: C9.1, R9.1, U16.21 (I10)
D11: C10.1, R10.1, U16.20 (I11)
D12: C13.1, R13.1, U16.19 (I12)
D13: C14.1, R14.1, U16.18 (I13)
D14: C15.1, R15.1, U16.17 (I14)
D15: C16.1, R16.1, U16.16 (I15)
Data_IR_sensor: J4.1, U16.1 (COM)
E: J4.11, U16.15 (~E)
GND: C1.2, C2.2, C3.2, C4.2, C5.2, C6.2, C7.2, C8.2, C9.2, C10.2, C11.2, C12.2, C13.2, C14.2, C15.2, C16.2, Camera_RST.2, J1.4, J3.4, J4.10, U1.2 (GND), U2.2 (GND), U3.2 (GND), U4.2 (GND), U5.2 (GND), U6.2 (GND), U7.2 (GND), U8.2 (GND), U9.2 (GND), U10.2 (GND), U11.2 (GND), U12.2 (GND), U13.2 (GND), U14.2 (GND), U15.2 (GND), U16.12 (GND), U17.2 (GND)
IR_Data1_Upside: J2.4, J4.13
IR_Data2_Upside: J2.3, J4.15
IR_Data3_Upside: J2.2, J4.17
IR_Data4_Upside: J2.1, J4.19
IR_Data5_Upside: J3.1, J4.21
IR_Data6_Upside: J3.2, J4.2
IRout0: R3.2, U17.1 (OUT)
IRout1: R4.2, U1.1 (OUT)
IRout2: R1.2, U2.1 (OUT)
IRout3: R2.2, U3.1 (OUT)
IRout4: R5.2, U4.1 (OUT)
IRout5: R6.2, U5.1 (OUT)
IRout6: R7.2, U6.1 (OUT)
IRout7: R8.2, U7.1 (OUT)
IRout8: R11.2, U8.1 (OUT)
IRout9: R12.2, U9.1 (OUT)
IRout10: R9.2, U10.1 (OUT)
IRout11: R10.2, U11.1 (OUT)
IRout12: R13.2, U12.1 (OUT)
IRout13: R14.2, U13.1 (OUT)
IRout14: R15.2, U14.1 (OUT)
IRout15: R16.2, U15.1 (OUT)
LCD-TeensyD10: J4.12, SW3.1
LCD-TeensyD11: J4.14, SW1.1
LCD-TeensyD12: J4.16, SW2.1
RST: Camera_RST.1, J4.6
S0: J4.3, U16.10 (S0)
S1: J4.5, U16.11 (S1)
S2: J4.7, U16.14 (S2)
S3: J4.9, U16.13 (S3)
SCL_LCD: J1.2, J4.18
SDA_LCD: J1.1, J4.20
Start_switch: J4.4, SW5.2

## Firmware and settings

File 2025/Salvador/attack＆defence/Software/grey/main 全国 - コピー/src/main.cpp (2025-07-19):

#include <Arduino.h>
#include <Adafruit_BNO055.h>
#include <Adafruit_Sensor.h>
#include <utility/imumaths.h>
#include <SPI.h>
#include <Servo.h>
#include <engelline.hpp>
#include "engelline.cpp"

#include <motor.h>
#include "vector.cpp"
#include <kicker.hpp>
#include "kicker.cpp"

#include <oled.h>
#include <linecul.h>

#define STARTPIN 3
#define role_changepin 36
#define camera_changepin 35
#define oled_changepin 34

#define front_line 9

#define TEST 32
#define TOUCH 13
#define kicker 30

#define communication1 27
#define communication2 26

//////oled関連///////////////////////////////////////////////////////////
int move_speed = 100;

int oled_start_;
bool start_sceen = true;
int oled_start_time;
bool oled_reset = false;

/// 共通 /////////////////////////////////////////////////////////////
// ボタン
int Start;
int role_change;
int camera_change;
int oled_change;

// ball
int IR_dir;
int IR_dis;

// kicker
int touch;
int kick_time;
int kick_test_time;
Kicker kicker_; // Kickerクラスのオブジェクトを作成

// cammera
int court_dir;
int yellow_dir;
int yellow_dis;
int blue_dir;
int blue_dis;
int atack_goal_dis;
int defence_goal_dis;

// time
int serial_count = 0;

/// アタッカー ////////////////////////////////////////////////////
int line_time_all;
int line_time_deep;

int goal_gyro_dir;
bool goal_mode;

long RandomNumber; // 「RandomNumber」をlongで変数宣言
bool random_first = true;
bool start_first = true;

int kick_off_time;
int kick_touch_time;

/// ゴールキーパー ///////////////////////////////////////////////

int line_start_;

int line_re;
bool line_research = true;
int line_bit_serial;
bool line_val = false;
int IR_line_change;
int goal_line_change;
int go_line = 500;
int goal_dir_leave = 500;

int IR_pre_dis = 0;
int IR_new_dis = 0;
int IR_dif = 0;
int IR_dif_sum = 0;
int ball_time;

int com_mode = 0;

int rulu_time = 0;
int rulu_pre_time = 0;
bool KICK_fin = true;
int mode_atack_pin;
bool atack_test = false;
bool own_goal = false;

//////////////////////////////////////////////////////////////////
void select_pid()
{
  if (atack_goal_dir == 300)
  {
    PID_mode = 0;
    move_speed = 90;
    goal_mode = true;
  }
  else
  {
    if (-10 <= goal_gyro_dir && goal_gyro_dir <= 10) // マイナス４０、４２は中立点
    {
      goal_mode = true;
      PID_mode = 0;
      move_speed = 90;
    }
    else if (-10 < goal_gyro_dir && goal_gyro_dir < -25 && goal_mode == true)
    {
      goal_mode = true;
      PID_mode = 0;
      move_speed = 90;
    }
    else if (-10 < goal_gyro_dir && goal_gyro_dir < -25 && goal_mode == false)
    {
      goal_mode = false;
      PID_mode = 1;
      move_speed = 65;
    }
    else if (goal_gyro_dir <= -25)
    {
      goal_mode = false;
      PID_mode = 1;
      move_speed = 65;
    }
    else if (10 < goal_gyro_dir && goal_gyro_dir < 25 && goal_mode == true)
    {
      goal_mode = true;
      PID_mode = 0;
      move_speed = 90;
    }
    else if (10 < goal_gyro_dir && goal_gyro_dir < 25 && goal_mode == false)
    {
      goal_mode = false;
      PID_mode = 1;
      move_speed = 65;
    }
    else if (goal_gyro_dir >= 25)
    {
      goal_mode = false;
      PID_mode = 1;
      move_speed = 65;
    }
  }
}

void setup()
{
  analogWriteResolution(10);

  pinMode(STARTPIN, INPUT_PULLDOWN);
  pinMode(role_changepin, INPUT_PULLDOWN);
  pinMode(camera_changepin, INPUT_PULLDOWN);
  pinMode(oled_changepin, INPUT_PULLDOWN);

  pinMode(TEST, OUTPUT);
  pinMode(TOUCH, INPUT_PULLDOWN);
  pinMode(kicker, OUTPUT);
  pinMode(resetpin, INPUT_PULLDOWN);
  pinMode(front_line, INPUT);
  oled_setup();
  kicker_.init(32, 30); // Kickerクラスのsetupを呼ぶ

  Serial.begin(115200);

  Serial1.begin(115200); // motor
  Serial1.setTimeout(10);

  Serial2.begin(115200); // IR
  Serial2.setTimeout(10);

  Serial3.begin(115200); // camera
  Serial3.setTimeout(10);

  Serial5.begin(115200); // line
  Serial5.setTimeout(10);

  if (!bno.begin(OPERATION_MODE_IMUPLUS))
  {
    Serial.print("Ooops, no BNO055 detected ...");
    while (1)
      ;
  }
  bno.setExtCrystalUse(true);
}
void attacker_setup()
{
  process_engelline();
  atack_goal_dir = atack_goal_dir * -1;
  goal_gyro_dir = atack_goal_dir - gyro_deg;

  if (IR_dir < 0)
  {
    IR_dir += 360;
  }
}

void attacker()
{
  if (line_bit > 0 || front_line_val > LINE_FRONT)
  {
    select_pid();
    LINE_reaction.start(); // line timer スタート
    LINE_reaction.tick();
    line_time_all = LINE_reaction.get_value();
    Move_Deg(court_dir, 100);
  }
  else
  {
    LINE_reaction.tick();
    line_time_all = LINE_reaction.get_value();
    if (line_time_all < 100 && line_time_all > 0)
    {
      select_pid();
      LINE_reaction.tick();
      line_time_all = LINE_reaction.get_value();
      Move_Deg(court_dir, 100);
    }
    else
    {
      LINE_reaction.reset();
      line_time_all = LINE_reaction.get_value();
      if (IR_dir == 500)
      {
        PID_mode = 0;
        Move_Deg(0, 0);
      }
      else
      {
        if (touch == 1)
        {
          PID_mode = 1;
          if (IR_dir < 20 || IR_dir > 340)
          {
            if (atack_goal_dis < 118)
            {
              if (atack_goal_dir <= 15 && atack_goal_dir >= -15)
              {
                kicker_.kick(200, 50);
                KICK_fin = false;
              }
            }
            else
            {
              kicker_.kick(200, 250);
              KICK_fin = false;
            }
          }
          Move_Deg(0, move_speed);
        }
        else
        {
          KICK.reset();
          if (IR_dis > 11)
          {
            select_pid();
            Move_Deg(IR_dir, move_speed);
          }
          else
          {
            if (IR_dir < 17)
            {
              select_pid();
              Move_Deg(0, move_speed);
            }
            else if (IR_dir < 30)
            {
              select_pid();
              if (PID_mode == 0)
              {
                Move_Deg(IR_dir + 35, move_speed);
              }
              else if (PID_mode == 1)
              {
                Move_Deg(IR_dir + 50, move_speed);
              }
            }
            else if (IR_dir < 60)
            {
              select_pid();
              if (PID_mode == 0)
              {
                Move_Deg(IR_dir + 65, move_speed);
              }
              else if (PID_mode == 1)
              {
                Move_Deg(IR_dir + 60, move_speed);
              }
            }
            else if (IR_dir < 160)
            {
              PID_mode = 0;
              move_speed = 80;
              Move_Deg(IR_dir + 50, move_speed);
            }
            else if (IR_dir < 180)
            {
              PID_mode = 0;
              move_speed = 80;
              Move_Deg(IR_dir + 45, move_speed);
            }
            else if (IR_dir < 200)
            {
              PID_mode = 0;
              move_speed = 80;
              Move_Deg(IR_dir - 45, move_speed);
            }
            else if (IR_dir < 300)
            {
              PID_mode = 0;
              move_speed = 80;
              Move_Deg(IR_dir - 50, move_speed);
            }
            else if (IR_dir < 330)
            {
              select_pid();
              if (PID_mode == 0)
              {
                Move_Deg(IR_dir - 65, move_speed);
              }
              else if (PID_mode == 1)
              {
                Move_Deg(IR_dir - 60, move_speed);
              }
            }
            else if (IR_dir < 343)
            {
              select_pid();
              if (PID_mode == 0)
              {
                Move_Deg(IR_dir - 35, move_speed);
              }
              else if (PID_mode == 1)
              {
                Move_Deg(IR_dir - 50, move_speed);
              }
            }
            else
            {
              PID_mode = 0;
              Move_Deg(0, move_speed);
            }
          }
        }
      }
    }
  }
  // if (atack_goal_dir == -500)
  // {
  //   goal_gyro_dir = atack_goal_dir - gyro_deg;
  // }
  // else
  // {
  //   goal_gyro_dir = atack_goal_dir - gyro_deg + 180;
  // }

  // Serial.print("line_time");
  // Serial.print(line_time_all);
  // Serial.print("\t");
}

void defence_setup()
{
  if (defence_goal_dir < 500)
  {
    goal_dir_leave = defence_goal_dir;
  }
  if (defence_goal_dir >= 0)
  {
    goal_line_change = defence_goal_dir - 180;
  }
  else
  {
    goal_line_change = defence_goal_dir + 180;
  }

  // gyro();

  if (line_bit > 0)
  {
    line_val = true;
  }
  else
  {
    line_val = false;
  }
  if (mass1 == mass2)
  {
    mass2 = 500;
  }
  atack_goal_dir = atack_goal_dir * -1;
  IR_line_change = IR_dir;
  if (IR_line_change < 0)
  {
    IR_line_change += 360;
  }
}

void defence()
{

  PID_mode = 0;
  move_speed = 45;
  if (com_mode == 0)
  {

    PID_mode = 0;
    if (line_start_ == 0)
    {
      if (abs(IR_dir) > 135)
      {
        com_mode = 2;
        own_goal = true;
      }

      if (defence_goal_dir == 500)
      {
        if (line_bit > 0)
        {
          Move_Deg(court_dir, 80);
        }
        else
        {

          Move_Deg(180, 80);
        }
      }
      else
      {
        if (line_bit > 0)
        {
          if (defence_goal_dis > 110)
          {
            Move_Deg(court_dir, 80);
          }
          else
          {
            com_mode = 1;
          }
        }
        else
        {

          Move_Deg(defence_goal_dir, 80);
        }
      }
    }
  }
  else if (com_mode == 1)
  {
    PID_mode = 0;
    if (defence_goal_dir == 500)
    {
      // Move_Deg(180, 40);
      com_mode = 0;
    }
    else
    {
      // com_mode = 0
      if (defence_goal_dir > 90 && defence_goal_dis > 100)
      {
        com_mode = 0;
      }
      else if (defence_goal_dir < -90 && defence_goal_dis > 100)
      {
        com_mode = 0;
      }

      if (line_val == true)
      {

        if (mass1 < 500 && mass2 == 500 && mass3 == 500)
        {
          go_line = mass1;
          if (abs(defence_goal_dir - IR_dir) >= 45)
          {
            if (IR_dir > 0)
            {
              Move_Deg(mass1, 80);
            }
            else
            {
              Move_Deg(mass1, 80);
            }
          }
          else
          {
            Move_Deg(mass1, 20);
          }
        }
        else if (mass1 < 500 && mass2 < 500 && mass3 == 500)
        {
          rulu_time = RULU.get_value();

          if (abs(defence_goal_dir) >= 135)
          {
            if (IR_dis <= 8)
            {
              if (mass1 < 500 && mass2 < 500)
              {
                if (goal_line_change - 45 < IR_dir && goal_line_change + 45 > IR_dir)
                { //
                  RULU.start();
                  RULU.tick();
                  if (rulu_time >= 2000)
                  {
                    rulu_time = 0;
                    RULU.reset();
                    com_mode = 2;
                  }
                }
              }
              else
              {
                rulu_time = 0;
                RULU.reset();
              }
            }
            else
            {
              rulu_time = 0;
              RULU.reset();
            }
          }
          else
          {
            rulu_time = 0;
            RULU.reset();
          }

          if (mode_line == 0) ////////////////////////////////////////////////////////////////////////////////////////////////////////////////////////////////////
          {
            if (IR_dir >= -180 && IR_dir < 500)
            {

              if (goal_line_change - 130 > IR_dir)
              {
                Move_Deg(mass2, 20);
              }
              else if (goal_line_change - 70 > IR_dir)
              {
                Move_Deg(mass2, 70);
              }
              else if (goal_line_change - 40 > IR_dir)
              {
                Move_Deg(mass2, 60);
              }
              else if (goal_line_change - 20 > IR_dir)
              {
                Move_Deg(mass2, 50);
              }
              else if (goal_line_change + 10 > IR_dir)
              {
                Move_Deg(0, 0);
              }
              else if (goal_line_change + 40 > IR_dir)
              {
                Move_Deg(mass1, 50);
              }
              else if (goal_line_change + 50 > IR_dir)
              {
                Move_Deg(mass1, 60);
              }
              else if (goal_line_change + 120 > IR_dir)
              {
                Move_Deg(mass1, 70);
              }
              else
              {
                Move_Deg(mass1, 20);
              }
            }
            else
            {
              // mass1 = line_dir_stop(mass1, mass2);
              if (goal_line_change > 7)
              {
                Move_Deg(mass2, move_speed + 10);
              }
              else if (goal_line_change > -7)
              {
                Move_Deg(0, 0);
              }
              else
              {
                Move_Deg(mass1, move_speed + 10);
              }
            }
          }
          else if (mode_line == 3) ////////////////////////////////////////後ろ//////////////////////mode3
          {

            if (defence_goal_dir > 0)
            {
              if (abs(IR_dir) > 135)
              {
                Move_Deg(180, 20);
              }
              else
              {
                if (goal_line_change - 6 > IR_dir)
                {
                  if (abs(mass1 - 0) < abs(mass2 - 360))
                  {
                    Move_Deg(mass2, 20);
                  }
                  else
                  {
                    Move_Deg(mass1, 20);
                  }
                }
                else if (goal_line_change < IR_dir)
                {
                  if (abs(mass1 - 0) < abs(mass2 - 360))
                  {
                    Move_Deg(mass1, 50);
                  }
                  else
                  {
                    Move_Deg(mass2, 50);
                  }
                }
                else
                {
                  Move_Deg(0, 0);
                }
              }
            }
            else
            {
              if (abs(IR_dir) > 135)
              {
                Move_Deg(180, 20);
              }
              else
              {
                if (goal_line_change > IR_dir)
                {

                  if (abs(mass1 - 0) < abs(mass2 - 360))
                  {
                    Move_Deg(mass1, 60);
                  }
                  else
                  {
                    Move_Deg(mass2, 60);
                  }
                }
                else if (goal_line_change + 10 < IR_dir)
                {
                  if (abs(mass1 - 0) < abs(mass2 - 360))
                  {
                    Move_Deg(mass2, 20);
                  }
                  else
                  {
                    Move_Deg(mass1, 20);
                  }
                }
                else
                {
                  Move_Deg(0, 0);
                }
              }
            }
          }
          else if (mode_line == 4) //////////////////////////////////////////////////左右////////////mode4
          {
            if (IR_dir == 500)
            {
              if (goal_line_change > 7)
              {
                Move_Deg(mass2, move_speed);
              }
              else if (goal_line_change > -7)
              {
                Move_Deg(0, 0);
              }
              else
              {

                Move_Deg(mass1, move_speed);
              }
            }
            else
            {
              if (IR_dis <= 8)
              {
                if (goal_line_change - 117 > IR_dir)
                {
                  Move_Deg(270, 20);
                }
                else if (goal_line_change - 80 > IR_dir)
                {
                  Move_Deg(270, 90);
                }
                else if (goal_line_change - 40 > IR_dir)
                {
                  Move_Deg(270, 80);
                }
                else if (goal_line_change - 11 > IR_dir)
                {
                  Move_Deg(270, 60);
                }
                else if (goal_line_change + 20 > IR_dir)
                {
                  Move_Deg(0, 0);
                }
                else if (goal_line_change + 40 > IR_dir)
                {
                  Move_Deg(90, 60);
                }
                else if (goal_line_change + 90 > IR_dir)
                {
                  Move_Deg(90, 80);
                }
                else if (goal_line_change + 120 > IR_dir)
                {
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
void loop()
{

  is_line_detected();
  // is_line_evacuation();
  is_previous_line_detected();
  kicker_.loop(); // Kickerクラスのloopを呼ぶ
  digitalWrite(TEST, HIGH);
  touch = digitalRead(TOUCH);
  Start = digitalRead(STARTPIN);
  role_change = digitalRead(role_changepin);
  camera_change = digitalRead(camera_changepin);
  oled_change = digitalRead(oled_changepin);
  front_line_val = analogRead(front_line);
  ///////////oled関係
  oled_button();
  if (digitalRead(oled_start_pin) == 1)
  {
    oled_reset = false;
    OLED.start();
    OLED.tick();
    oled_start_time = OLED.get_value();
    if (oled_start_time > 50)
    {
      Gyro_cal(gyro_deg);
      IR_dir_cal(IR_dir);
      Line_cal(line_bit, front_line_val);
      Camera_dir_cal(yellow_dir, blue_dir, court_dir);
      oled_main();
      oled_start_time = 0;
      OLED.reset();
    }
  }
  else
  {
    if (oled_reset == false)
    {
      reset_oled();
      oled_reset = true;
      screen_num = 0;
    }
  }

  //////////値の読み取り
  gyro();

  while (Serial2.available() > 0) // ir
  {
    IR_dir = Serial2.readStringUntil('a').toInt();
    IR_dis = Serial2.readStringUntil('b').toInt();
  }

  while (Serial3.available() > 0) // camera
  {
    court_dir = Serial3.readStringUntil('a').toInt();
    yellow_dir = Serial3.readStringUntil('b').toInt();
    yellow_dis = Serial3.readStringUntil('c').toInt();
    blue_dir = Serial3.readStringUntil('d').toInt();
    blue_dis = Serial3.readStringUntil('e').toInt();
  }

  while (Serial5.available() > 0) // line
  {
    line_bit = Serial5.readStringUntil('a').toInt();
  }
  mass1 = 500;
  mass2 = 500;
  mass3 = 500;
  line_main();

  defence_goal_dir = yellow_dir;
  defence_goal_dis = yellow_dis;
  atack_goal_dir = blue_dir;
  atack_goal_dis = blue_dis;

  // defence_goal_dir = blue_dir;
  // defence_goal_dis = blue_dis;
  // atack_goal_dir = yellow_dir;
  // atack_goal_dis = yellow_dis;

  if (role_change == 0)
  {
    attacker_setup();
    if (atack_goal_dir == -500)
    {
      PID_mode = 0;
    }
  }
  else
  {
    defence_setup();
  }

  // if (digitalRead(communication1) == 1 || digitalRead(communication2) == 1)
  // {
  if (Start == 1)
  {
    if (role_change == 0)
    {
      attacker();
    }
    else
    {
      defence();
    }
  }
  else
  {
    move(0, 0, 0, 0);
  }
  // }
  // else
  // {
  //   move(0, 0, 0, 0);
  // }

  Serial.print("IR_dir ");
  Serial.print(IR_dir);
  Serial.print("   ");
  Serial.print("\t");

  // Serial.print("IR_dis ");
  // Serial.print(IR_dis);
  // Serial.print("   ");
  // Serial.print("\t");

  Serial.print("line_bit ");
  Serial.print(line_bit);
  Serial.print("   ");
  Serial.print("\t");

  Serial.print("gyro_dir ");
  Serial.print(gyro_deg);
  Serial.print("   ");
  Serial.print("\t");

  Serial.print("goal_gyro_dir ");
  Serial.print(goal_gyro_dir);
  Serial.print("   ");
  Serial.print("\t");

  // Serial.print("court_dir ");
  // Serial.print(court_dir);
  // Serial.print("   ");
  // Serial.print("\t");

  Serial.print("goal_dir ");
  Serial.print(atack_goal_dir);
  Serial.print("   ");
  Serial.print("\t");

  // Serial.print("line_change ");
  // Serial.print(goal_line_change);
  // Serial.print("   ");

  // Serial.print("atack_goal_dir ");
  // Serial.print(atack_goal_dir);
  // Serial.print("   ");
  // Serial.print("\t");

  // Serial.print("goal_dis ");
  // Serial.print(defence_goal_dis);
  // Serial.print("   ");
  // Serial.print("\t");

  // Serial.print("front ");
  // Serial.print(front_line_val);
  // Serial.print("   ");
  // Serial.print("\t");

  // Serial.print("camera_change ");
  // Serial.print(camera_change);
  // Serial.print("   ");
  // Serial.print("\t");

  // Serial.print("role_change ");
  // Serial.print(role_change);
  // Serial.print("   ");
  // Serial.print("\t");
  // Serial.print("com ");
  // Serial.print(com_mode);
  // Serial.print("   ");
  // Serial.print("side ");
  // Serial.print(side_line);
  // Serial.print("   ");
  // Serial.print("evacuation_deg ");
  // Serial.print(line_evacuation_deg);
  // if (is_halfout)
  // {

  //   Serial.print("halfout");
  // }
  // Serial.print("kick_touch_time ");
  // Serial.print(kick_touch_time);
  // Serial.print("   ");
  // Serial.print("\t");
  // Serial.print("kick_off_time ");
  // Serial.print(kick_off_time);
  // Serial.print("   ");
  // Serial.print("IR_li ");
  // Serial.print(IR_line_change);
  // Serial.print("   ");
  // Serial.print("rulu_time ");
  // Serial.print(rulu_time);
  // Serial.print("   ");
  // Serial.print("\t");
  Serial.println("\t");
}

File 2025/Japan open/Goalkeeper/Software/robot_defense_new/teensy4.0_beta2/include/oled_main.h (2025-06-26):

#include <Arduino.h>
#include <Wire.h>
#include <Adafruit_GFX.h>
#include <Adafruit_SSD1306.h>
#include <timer.h>

//////////////画像/////////////////
#include <oled_aegis.h>

// 左10　真ん中12　右11

#define left_button 10
#define right_button 11
#define center_button 12

// コンパイル時にヘッダーファイルが適切に編集されていない場合に
// "Height incorrect, please fix Adafruit_SSD1306.h!"
// というエラーを表示するための記述
#if (SSD1306_LCDHEIGHT != 64)
// #error("Height incorrect, please fix Adafruit_SSD1306.h!");
#endif

// RSTピンがない互換品を使用するので-1を指定
#define SCREEN_WIDTH 128 // OLED display width, in pixels
#define SCREEN_HEIGHT 64 // OLED display height, in pixels

// Declaration for an SSD1306 display connected to I2C (SDA, SCL pins)
#define OLED_RESET -1 // Reset pin # (or -1 if sharing Arduino reset pin)
Adafruit_SSD1306 display(SCREEN_WIDTH, SCREEN_HEIGHT, &Wire, OLED_RESET);

#define oled_start_pin 4
int IR_dir_x;
int IR_dir_y;
int IR_dir_screen;

int gyro_x;
int gyro_y;
int gyro_screen;

int line_x;
int line_y;
int line_screen;
int line_det;

int yellow_x;
int yellow_y;
int yellow_screen;

int blue_x;
int blue_y;
int blue_screen;

int green_x;
int green_y;
int green_screen;

int screen_num = 0;
int floar;

int left_total;
int right_total;
int center_total;


int mode_change = 0;

void oled_aegis()
{

  // 画面表示をクリア
  display.clearDisplay();

  display.drawBitmap(0, 0, bitmap_aegis, LOGO_WIDTH, LOGO_HEIGHT, SSD1306_WHITE);

  // 描画バッファの内容を画面に表示
  display.display();
}
void IR_dir_cal(int IR_dir){
  IR_dir_x = sin(radians(IR_dir)) * 20;
  IR_dir_y = cos(radians(IR_dir)) * 20;
  if(IR_dir == 500){
    IR_dir_x = 0;
    IR_dir_y = 0;
  }
  IR_dir_screen = IR_dir;
}

void Gyro_cal(int gyro_dir){
  gyro_x = sin(radians(gyro_dir)) * 20;
  gyro_y = cos(radians(gyro_dir)) * 20;

  gyro_screen = gyro_dir;

}

void Line_cal(int line, int line_dir){
  line_x = sin(radians(line_dir)) * 20;
  line_y = cos(radians(line_dir)) * 20;

  line_screen = line_dir;
  line_det = line;
  if(line_dir == 500){
    line_x = 0;
    line_y = 0;
  }

}
void Camera_dir_cal(int goal_yellow,int goal_blue,int cout_green){
  yellow_x = sin(radians(goal_yellow)) * 20;
  yellow_y = cos(radians(goal_yellow)) * 20;

  yellow_screen = goal_yellow;

  blue_x = sin(radians(goal_blue)) * 20;
  blue_y = cos(radians(goal_blue)) * 20;

  blue_screen = goal_blue;

  green_x = sin(radians(cout_green)) * 20;
  green_y = cos(radians(cout_green)) * 20;

  green_screen = cout_green;

}

void oled_setup()
{
  // I2Cアドレスは使用するディスプレイに合わせて変更する
  display.begin(SSD1306_SWITCHCAPVCC, 0x3C);
  pinMode(left_button, INPUT_PULLDOWN);
  pinMode(right_button, INPUT_PULLDOWN);
  pinMode(center_button, INPUT_PULLDOWN);
  pinMode(oled_start_pin, INPUT_PULLDOWN);
}

#define max_sceen_num_0 3
#define max_sceen_num_1 7
#define max_sceen_num_2 1
#define max_sceen_num_3 2
bool button_cool = true;
void oled_button()
{
  int button_time_left;
  int button_time_right;
  int button_time_center;
  bool button;

  left_total = digitalRead(left_button);
  right_total = digitalRead(right_button);
  center_total = digitalRead(center_button);
  
  button_time_left = BUTTON_left.get_value();
  BUTTON_left.tick();

  button_time_right = BUTTON_right.get_value();
  BUTTON_right.tick();
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

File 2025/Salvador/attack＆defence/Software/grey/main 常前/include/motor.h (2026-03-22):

#include <Arduino.h>
#include <acceleration.h>

int atack_goal_dir;
// int gyro_deg;
int gyro_data_pid;
float v_speed;

void breaking()
{
  Serial1.println("1R0002R0003R0004R000");
}

void move(int a, int b, int c, int d)
{
  int val = 0;
  int input[4] = {a, b, c, d};
  int output[4] = {0, 0, 0, 0};
  String StringA = "0";
  String StringB = "0";
  String StringC = "0";
  String StringD = "0";
  String StringX = "0";
  String StringY = "0";
  String StringZ = "0";
  String String0 = "0";

  StringX = String(1);
  val = input[0];
  if (val < 0 && val >= -100)
  {
    StringY = String('R');
    val = abs(val);
    StringZ = String(val);
  }
  else if (val >= 0 && val <= 100)
  {
    StringY = String('F');
    StringZ = String(val);
  }
  else
  {
    StringY = String('F');
    StringZ = String(0);
  }
  if (val < 10)
  {
    String0 = String("00");
    StringZ = String0 + StringZ;
  }
  else if (val < 100)
  {
    String0 = String('0');
    StringZ = String0 + StringZ;
  }
  else
  {
    String0 = String("");
  }
  StringA = StringX + StringY + StringZ;

  StringX = String(2);
  val = input[1];
  if (val < 0 && val >= -100)
  {
    StringY = String('R');
    val = abs(val);
    StringZ = String(val);
  }
  else if (val >= 0 && val <= 100)
  {
    StringY = String('F');
    StringZ = String(val);
  }
  else
  {
    StringY = String('F');
    StringZ = String(0);
  }
  if (val < 10)
  {
    String0 = String("00");
    StringZ = String0 + StringZ;
  }
  else if (val < 100)
  {
    String0 = String('0');
    StringZ = String0 + StringZ;
  }
  else
  {
  }
  StringB = StringX + StringY + StringZ;

  StringX = String(3);
  val = input[2];
  if (val < 0 && val >= -100)
  {
    StringY = String('R');
    val = abs(val);
    StringZ = String(val);
  }
  else if (val >= 0 && val <= 100)
  {
    StringY = String('F');
    StringZ = String(val);
  }
  else
  {
    StringY = String('F');
    StringZ = String(0);
  }
  if (val < 10)
  {
    String0 = String("00");
    StringZ = String0 + StringZ;
  }
  else if (val < 100)
  {
    String0 = String('0');
    StringZ = String0 + StringZ;
  }
  else
  {
  }
  StringC = StringX + StringY + StringZ;

  StringX = String(4);
  val = input[3];
  if (val < 0 && val >= -100)
  {
    StringY = String('R');
    val = abs(val);
    StringZ = String(val);
  }
  else if (val >= 0 && val <= 100)
  {
    StringY = String('F');
    StringZ = String(val);
  }
  else
  {
    StringY = String('F');
    StringZ = String(0);
  }
  if (val < 10)
  {
    String0 = String("00");
    StringZ = String0 + StringZ;
  }
  else if (val < 100)
  {
    String0 = String('0');
    StringZ = String0 + StringZ;
  }
  else
  {
  }
  StringD = StringX + StringY + StringZ;

  Serial1.println(StringA + StringB + StringC + StringD);
}

float get_max_value_in_array(float *ar) // 絶対値の個数
{
  float ret;

  for (int i = 0; i < 4; i++)
  {
    if (abs(ar[i] > ret))
    {
      ret = abs(ar[i]);
    }
  }

  return ret;
}

float val_P;
float val_D;
int PID_mode;

float pid_deviation; // 今回の実際角の偏差
float previous_pid_deviation;
int PID_gain(float P_gain, float D_gain, float P_gain_cam, int D_gain_cam, int outputdata, int PID_data, int limit)
// int PID_gain(float P_gain, float D_gain, float P_gain_cam, int D_gain_cam, int outputdata, int PID_data, int limit)
{
  int val_PID;
  int D_data;

  // 比例
  // val_P = (outputdata - 512.1) * P_gain;
  // PID_mode = 0;
  // PID_mode = 0;
  if (PID_mode == 1)
  {

    val_P = PID_data * P_gain_cam;
  }
  else
  {

    val_P = (outputdata)*P_gain; // マイナスけした
  }

  // 微分
  pid_deviation = val_P;
  val_D = pid_deviation - previous_pid_deviation;
  previous_pid_deviation = pid_deviation;

  if (PID_mode == 1)
  {

    D_data = D_gain_cam;
  }
  else
  {
    D_data = D_gain;
  }

  // 計算
  val_PID = (int)(max(min(val_P + val_D * D_gain, limit), -limit));

  return val_PID;
}

void Move_Deg(int deg, float power)
{
  float power_[4] = {0, 0, 0, 0};

  float multipli;
  float power_No1 = 0;
  float lost_power;

  int pid_val = PID_gain(1.5, 9, 0.2, 1.7, gyro_deg, atack_goal_dir, 40);
  // int pid_val = PID_gain(3.7, 8.5, 0.5, 9.5, gyro_deg, goal_dir, 40);
  // int pid_val = PID_gain(0.7,0.3, 0.5, 9.5, gyro_deg, goal_dir, 40);

  power_[0] = -sin((deg - 45) / 180.0 * 3.14) * power;  //+ pid_val
  power_[1] = sin((deg + 45) / 180.0 * 3.14) * power;   //- pid_val
  power_[2] = -sin((deg - 135) / 180.0 * 3.14) * power; //+ pid_val
  power_[3] = sin((deg + 135) / 180.0 * 3.14) * power;  //- pid_val

  for (int i = 0; i < 4; i++)
  {
    if (abs(power_[i]) >= power_No1)
    {
      power_No1 = abs(power_[i]);
    }
  }

  if (power_No1 != 0)
  {
    multipli = power / power_No1;

    for (int i = 0; i < 4; i++)
    {
      power_[i] = power_[i] * multipli;
    }
  }

  power_[0] += pid_val;
  power_[1] -= pid_val;
  power_[2] += pid_val;
  power_[3] -= pid_val;

  power_No1 = get_max_value_in_array(power_);

  if (power_No1 > 100)
  {
    lost_power = power_No1 - 100;

    for (int i = 0; i < 4; i++)
    {
      if (power_[i] > 0)
      {
        power_[i] = power_[i] - lost_power;
      }
      else
      {
        power_[i] = power_[i] + lost_power;
      }
    }
  }
  else
  {
    for (int i = 0; i < 4; i++)
    {
      power_[i] = max(min(power_[i], 100), -100);
    }
  }

  // Serial.print(power_[0]);
  // Serial.print("\t");
  // Serial.print(power_[1]);
  // Serial.print("\t");
  // Serial.print(power_[2]);
  // Serial.print("\t");
  // Serial.print(power_[3]);
  // Serial.print("\t");

  move((int)power_[0], (int)power_[1], (int)power_[2], (int)power_[3]);
}

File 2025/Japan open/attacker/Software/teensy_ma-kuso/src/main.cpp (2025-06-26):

#include <Arduino.h>
#include <Adafruit_BNO055.h>
#include <Adafruit_Sensor.h>
#include <utility/imumaths.h>
#include <SPI.h>
#include <Servo.h>

#include <motor.h>
#include "vector.cpp"
#include <oled.h>

Servo dribbler;

#define TEST 5
#define TOUCH 13
#define kicker 6
#define STARTPIN 23
#define camera_changepin 2
#define mode_changepin 3

//////oled関連/////
int oled_start_;
bool start_sceen = true;
int oled_start_time;
bool oled_reset = false;

/// プログラム///
int Start;
int kick_change;
int dribbler_change;

int IR_dir;
int IR_dis;
int before_ball;

int line_data;
int line_time_all;
int line_time_deep;

int touch;
int kick_time;
int kick_test_time;
int kick_camera_time;

int court_dir;
int yellow_dir;
int goal_dis;

int move_dir;
int court_IR_dir;
int goal_gyro_dir;
int goal_pid_select;

int dribbler_time;
int dribbler_gyro;

int kick_off_time;
int kick_touch_time;
int line_time_reaction;

bool KICK_fin = true;
bool goal_mode = true;

int move_speed;

long RandomNumber; // 「RandomNumber」をlongで変数宣言
bool random_first = true;
bool start_first = true;
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

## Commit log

2024-04-15 イージステスト
    適当
2024-07-14 かえました
2025-06-26 Create 2025_全国_goal_keeper
    ooo
2025-06-26 Delete 2025_全国_goal_keeper
    miss
2025-06-26 Create 2025_全国_goal_keeper
2025-06-26 Create Kicad
2025-06-26 Create 2024_japan_open_キリン
2025-06-26 英語
    英語にしたよ
2025-06-26 英語
    英語に変えた
2025-06-26 更新しました。
2025-06-28 寝よう！！
2025-06-28 基板データ
    [ESP32-B_Cu.gbr, ESP32-B_Mask.gbr, ESP32-B_Silkscreen.gbr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]
2025-06-28 クラファン
2025-06-28 イージスデータ
2025-06-28 プレゼンシート
    英語訳
2025-06-30 英語版
    訂正用
2025-06-30 camera
    カーペット用に変えました
2025-07-01 英語版
    コスト追加
2025-07-01 英語版
    カメラ
2025-07-01 camera
    あとカメラをカーペットから変更した。取材のインサート用
2025-07-01 加速度翻訳
    2回目
2025-07-01 移動平均終わり
2025-07-02 LINEのファイルを変えた
2025-07-02 フォルダ変更
2025-07-02 IRnoファイルがおかしい
2025-07-02 e英語版
    訂正
2025-07-03 Method/Production/Design final
    多分完成
2025-07-05 line基板
    追加しました
    [Line_front.kicad_pcb, Line_front.kicad_sch, Line_front.step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]
2025-07-06 yatta
    プログラむ変えました
2025-07-06 プレゼンシート
    修正済み
2025-07-07 あと少し
2025-07-08 flowchartを上げました。
    写真も載せないとーー
2025-07-08 忘れ物０で行こう!!
    [世界大会持ち物リスト最新版.xlsx]
2025-07-08 完成ほぼ
2025-07-09 Create de
2025-07-09 TDP用ファイルアップロード
    [Frame_underside v16.f3d, Frame_upperside v15.f3d, Line_front v4.f3d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]
2025-07-09 持ち物リスト完了
    [世界大会持ち物個人 ソフトウェア班.xlsx, 世界大会持ち物個人 ハードウェア班.xlsx]
2025-07-10 プログラム合わせた
2025-07-10 プレゼンシート
    太文字完成
2025-07-10 英語版
    修正
2025-07-10 持ち物リスト完成
    [世界大会持ち物個人 ソフトウェア班.xlsx, 世界大会持ち物個人 ハードウェア班.xlsx]
2025-07-11 Camera
    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
2025-07-16 プレゼン
    変更
2025-07-17 大会初日 アタッカー
2025-07-18 二日目頑張ろう！！！
2025-07-19 世界優勝!!!頑張ろう！
2026-04-10 ははははは
    [世界大会持ち物リスト.xlsx, 世界大会持ち物リスト最新版.xlsx, 世界大会持ち物個人 ソフトウェア班.xlsx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]
2026-04-14 kannsei
    a
    [Book1 (version 1).xlsb.xlsx, effort time.xlsx]
